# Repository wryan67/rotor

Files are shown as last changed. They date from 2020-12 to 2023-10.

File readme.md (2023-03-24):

Antenna Rotor Controller
------------------------
This program is designed to work with any rotor that uses a variable resistor for it's aspect indicator and limit swithes to prevent turning past the starting/stopping point.  Checkout the readme folder for display pinouts and a [[circuit diagram]](https://raw.githubusercontent.com/wryan67/rotor/main/schematics/drawio/rotor.png) for the system.

A special thanks to [PCBWay.com](http://www.pcbway.com) for supplying the professionally made PCB board!  

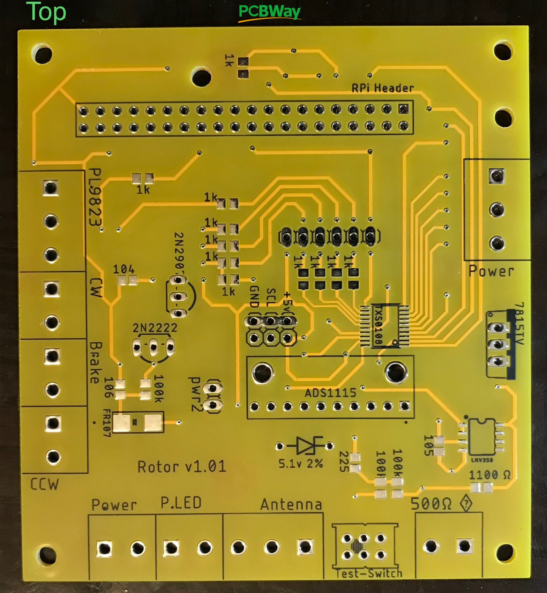
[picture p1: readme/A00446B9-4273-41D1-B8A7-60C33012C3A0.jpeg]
pcbway.com

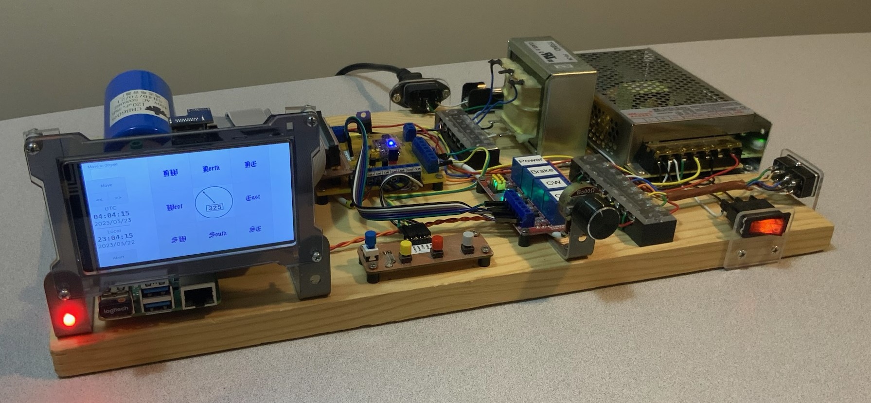
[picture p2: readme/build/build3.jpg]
build with pcbway.com


### Rotor Aspect Indicator
This system was designed around, and tested using a "Tail Twister" Model T2X - Rotator.  The Tail Twister utilizes a 500Ω variable resistor to ascertain the antenna's current direction.  The 500Ω variable resistor looks like this:  
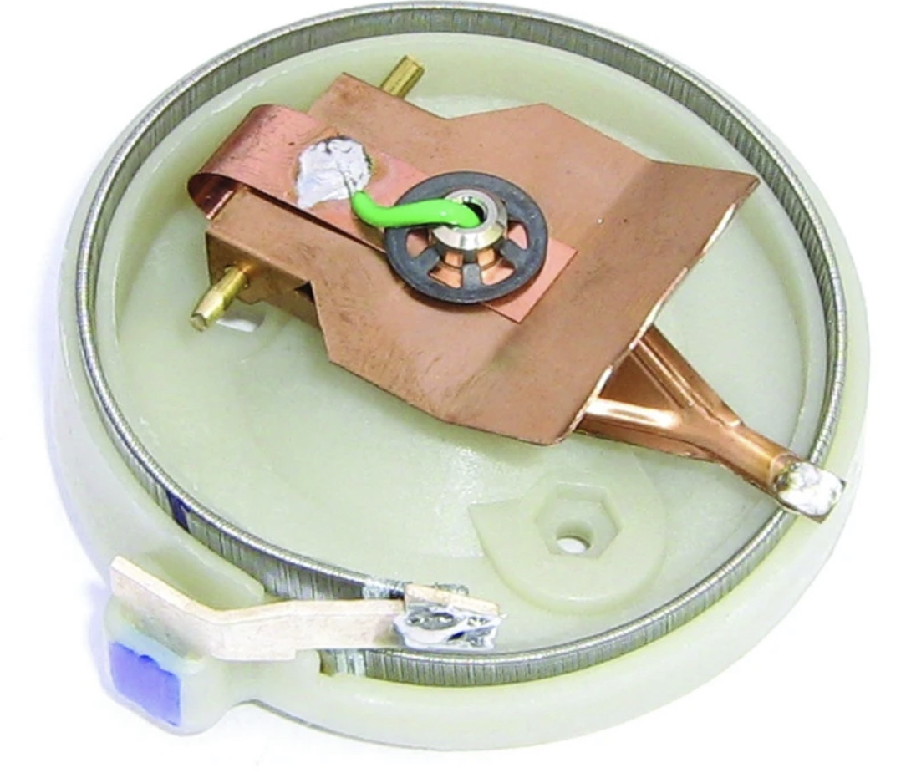
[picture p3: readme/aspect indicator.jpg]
aspect indicator


### Prerequisites:

Required system Libraries:

    $ sudo apt install libgtk-3-dev glade xdotool gawk ksh

Optional system Libraries:

    $ sudo apt vim tigervnc-standalone-server  tigervnc-xorg-extension tigervnc-scraping-server

## WiringPi

This step is required on RPi 4B.   Follow the instrctions on this website to upgrade to version 2.52

* http://wiringpi.com/wiringpi-updated-to-2-52-for-the-raspberry-pi-4b/

## Configuration

Using raspi-config, these options can be manuplated.  Enabling the I2C and SPI busses are required.

* System Options
  * Set the hostname
  * Set the pasword for the pi user
* Display Options
  * Disable screen blanking
* Interface Options
  * Enable the I2C bus
  * Enable the SPI bus
  * Enable the VNC server
  * Enable the SSH server

Starting raspi-config:

    $ sudo raspi-config

## Requirements

Overclocking the I2C bus is required to achive the desired 2500 samples per second.  Edit the /boot/config.txt file using:

Note: this step may need to be reapeated after installing a display device driver

    $ sudo vi /boot/config.txt 

Next, look for the i2c_arm parameter.  Note that if you've already enable the i2c bus via raspi-config, then you may have multiple lines in the config.txt file that have i2c_arm.  Look for the one that is uncommented.   If there are multiple "dtparam=i2c_arm=on" lines that are uncommented, comment out all but one.

    #dtparam=i2c_arm=on
    - or -
    dtparam=i2c_arm=on

Change it to:

    dtparam=i2c_arm=on,i2c_arm_baudrate=400000

## Disable warning lights
While you're in the boot config, you may want to disable the power indicator and lightning bolt indicator.  These indicators do not work properly on older RPi models due to an under sized capacitor on the RPi.  Newer models have larger capacitors, so if you have a brand new RPi 4, this step may not be necessary, but for the older RPi 4's, this indicator is extremely annoying. 

    $ sudo vi /boot/config.txt
    
    Append the following lines:
    
    # only affects power led operation
    dtparam=pwr_led_trigger=none
    dtparam=pwr_led_activelow=off
    # affects lightning bolt indicator
    avoid_warnings=1

### Required GIT Hub software:

Pleaase read the installation instructions carefully on each github project.  They're all similar, but non necessarially the same. 

* ADS1115 Library - https://github.com/wryan67/ads1115_rpi_lib    

      $ git clone https://github.com/wryan67/ads1115_rpi_lib.git

* NeoPixel Library - https://github.com/wryan67/neopixel_rpi_lib

       $ git clone https://github.com/wryan67/neopixel_rpi_lib.git       

* Log4Pi -https://github.com/wryan67/log4pi

       $ git clone https://github.com/wryan67/log4pi.git

### Download:

    git clone https://github.com/wryan67/rotor.git
    
### Compile:

    $ make
    
### Run:

Follow the instructions for autostart, then setup
    $ . scripts/set
    $ ./bin/rotor
    
### Auto Start on Boot

To start rotor on boot:

* Copy all files from the scripts folder (in this project) to $HOME/bin, then setup lxsession autostart using these commands:

      $ mkdir -p /home/pi/bin
      $ cp -p /home/pi/rotor/scripts/* /home/pi/bin
      $ cp -p /home/pi/rotor/bin/rotor /home/pi/bin
      $ cd /home/pi/bin
      $ sudo chown root rotor
      $ sudo chmod g+w  rotor
      $ sudo chmod u+s  rotor
      $ sudo chmod a+x  rotor
      $ mkdir -p ~/.config/lxsession/LXDE-pi/
      $ ln /home/pi/bin/autostart ~/.config/lxsession/LXDE-pi/autostart

### Build

This is the 2nd controller I built:
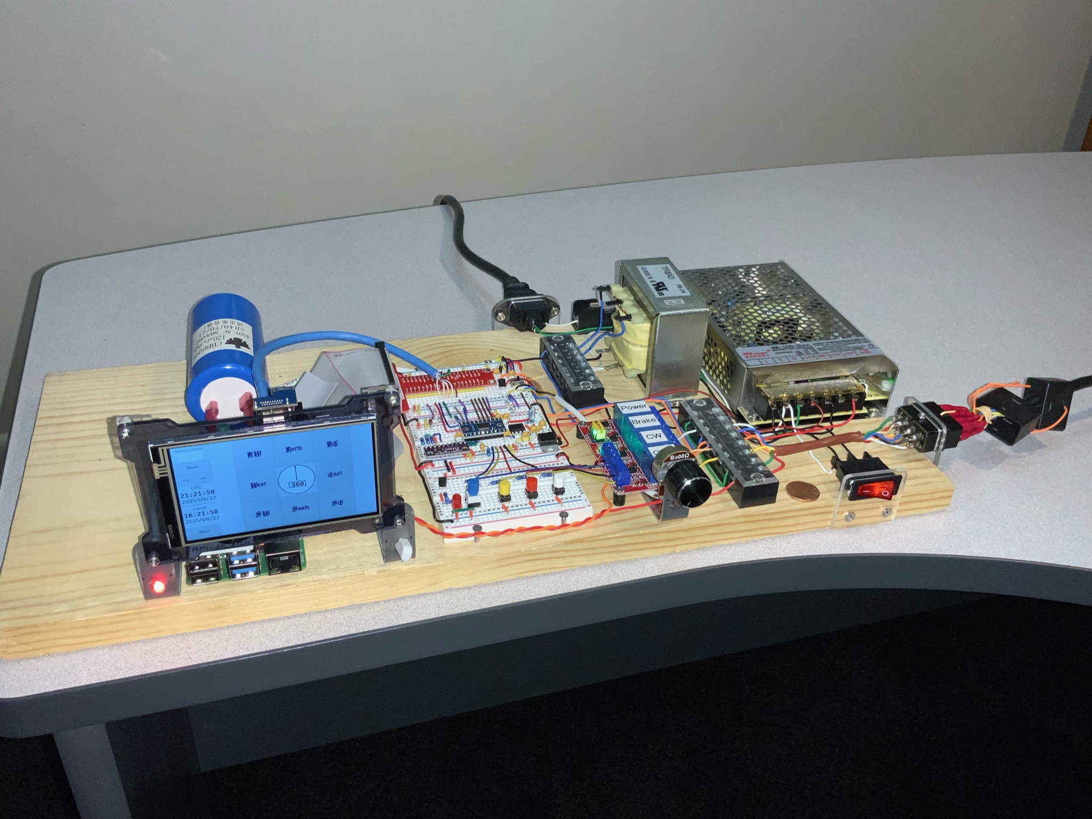
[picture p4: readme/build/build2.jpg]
build2


### Screenshots:

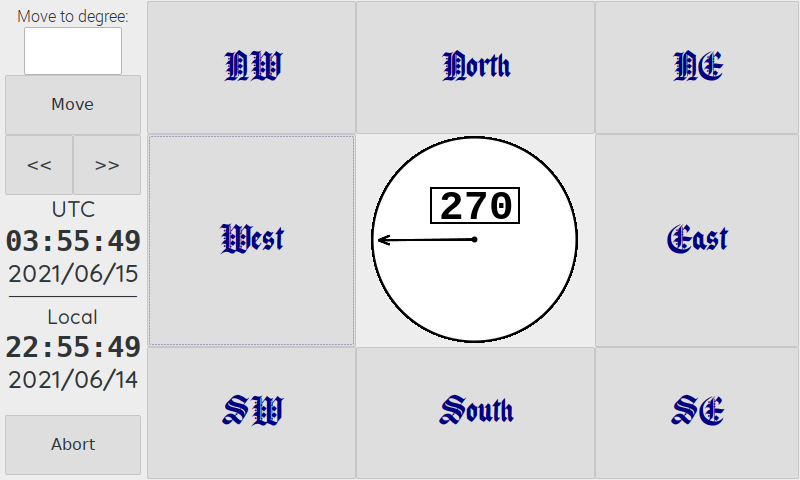
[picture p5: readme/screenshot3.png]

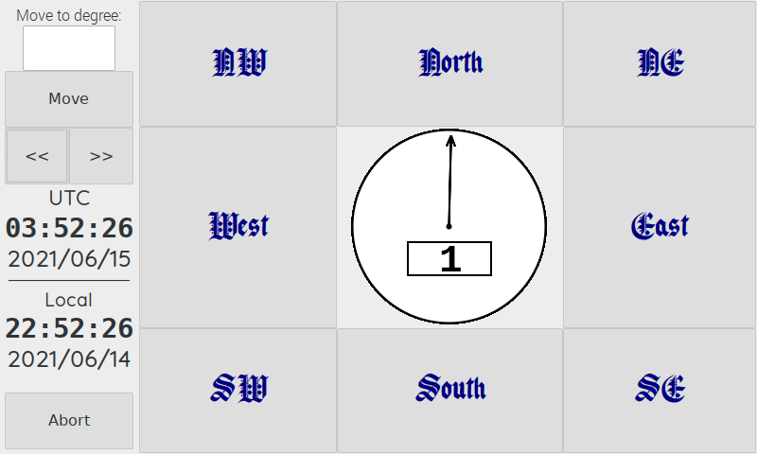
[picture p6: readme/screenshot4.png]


In order to access the configuration screens, click anywhere on the time clock.
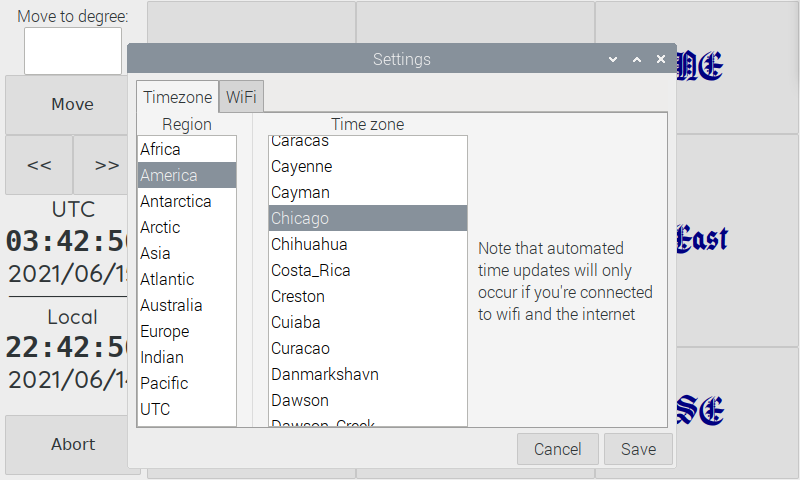
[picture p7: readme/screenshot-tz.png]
screenshot-tz

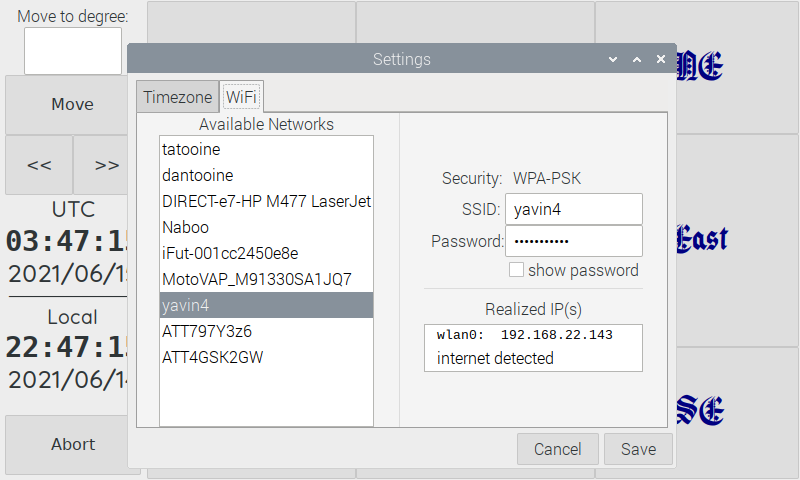
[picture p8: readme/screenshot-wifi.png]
screenshot-wifi


## Parts list
 
[Parts List](https://docs.google.com/spreadsheets/d/144g_11gsdxmeO28szwi-ss_1HRNR7ysNT9Fy6vf18YI/edit?usp=sharing)

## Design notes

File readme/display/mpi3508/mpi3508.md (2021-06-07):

## Driver install

https://github.com/goodtft/LCD-show

    $ git clone https://github.com/goodtft/LCD-show.git
    $ cd LCD-show
    $ sudo ./MPI3508-show

## Reference:  

https://raspberrypi.stackexchange.com/questions/61053/tft-lcd-3-5-display-with-inverted-axis

Invert instructions:

I had to swap both axis, and invert both of them as well, and then widen the input field
(reduce minx, increase max, reduce miny, increase maxy)

$ vi /etc/X11/xorg.conf.d/99-calibration.conf

    Section "InputClass"
    Identifier        "calibration"
    MatchProduct      "ADS7846 Touchscreen"
    Option "MinX"     "1834"
    Option "MaxX"     "62280"
    Option "MinY"     "61309"
    Option "MaxY"     "3738"
    Option "SwapXY"   "1" # unless it was already set to 1
    Option "InvertX"  "0"
    Option "InvertY"  "0"

    Option "TransformationMatrix" "0 -1 1 -1 0 1 0 0 1"

    EndSection

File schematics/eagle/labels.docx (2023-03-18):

J3

JP1

Console

+5 | +24 | Gnd

Gnd | P.SW | Gnd | P.led | Gnd | R.4 | R.3

LED
Ground
Power
CCW
Brake
CW

Ground
CW
Brake
CCW
Power
+5v

Gnd | +5v | Data | Gnd | CW | Gnd | Brk | Gnd | CCW

Data | Gnd

J10

Ads1115 addr

+5v
SCL
Gnd

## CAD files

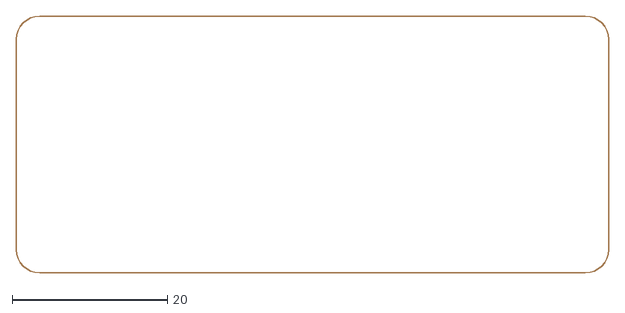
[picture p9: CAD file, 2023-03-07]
eagle/hat/hat.border.dxf
76.2 x 33.0

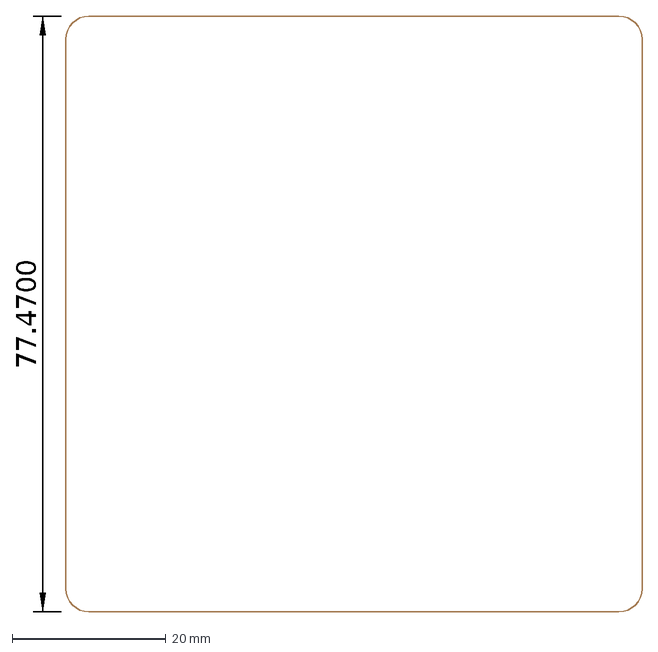
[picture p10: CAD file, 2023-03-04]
eagle/rotor.border.dxf
77.4700

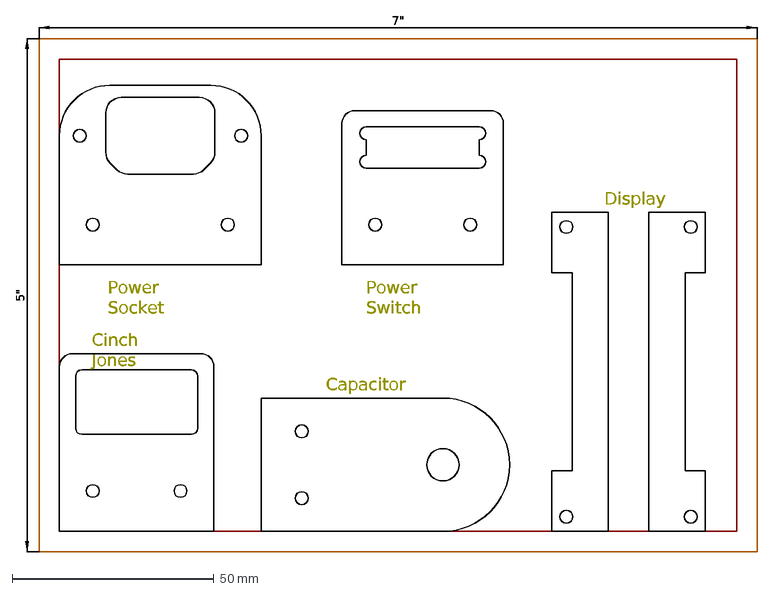
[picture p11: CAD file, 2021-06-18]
readme/rotor.brackets.dxf
7"
5"
Power Switch
Power Socket
Cinch Jones
Capacitor
Display

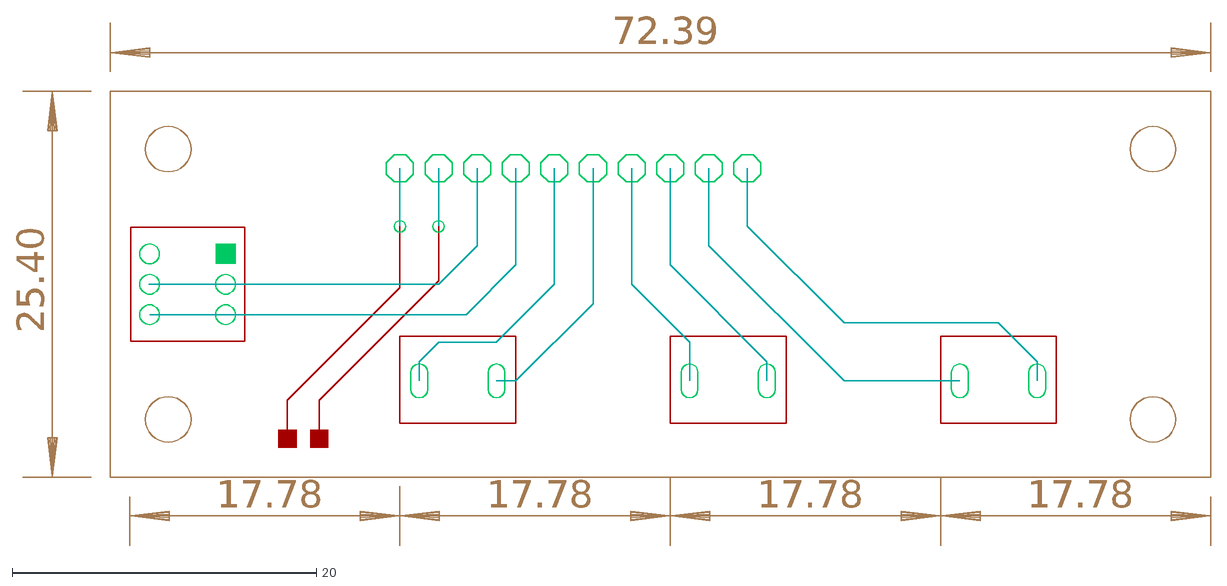
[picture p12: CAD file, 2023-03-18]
schematics/eagle/console/console.dxf
17.78
25.40
72.39

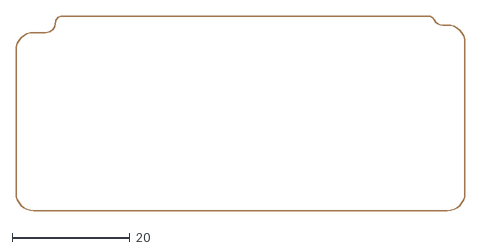
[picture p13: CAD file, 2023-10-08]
schematics/eagle/hat/hat.border.dxf
76.2 x 33.0

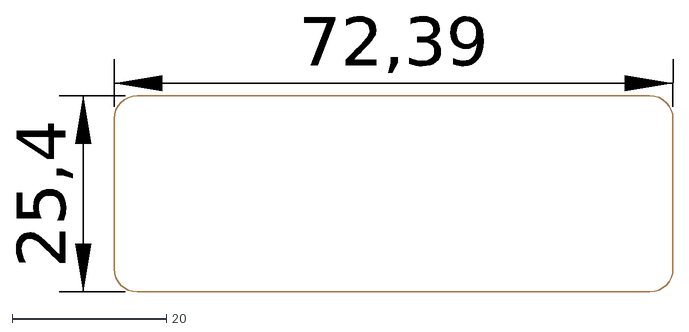
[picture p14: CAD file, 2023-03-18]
schematics/eagle/console/console.border.dxf
72,39
25,4

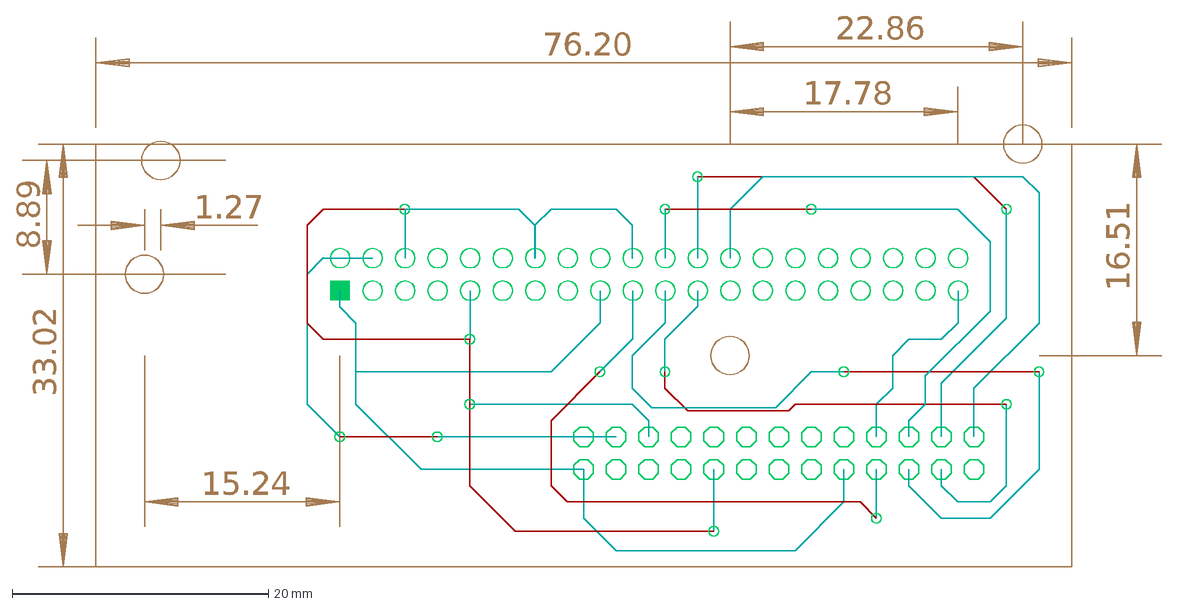
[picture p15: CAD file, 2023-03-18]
schematics/eagle/hat/hat.dxf
15.24
17.78
76.20
33.02
1.27
8.89
16.51
22.86

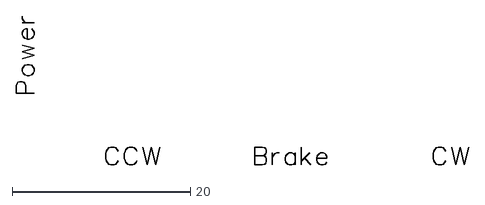
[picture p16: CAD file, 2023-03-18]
schematics/eagle/console/console.silkscreen.dxf
50.7 x 16.7

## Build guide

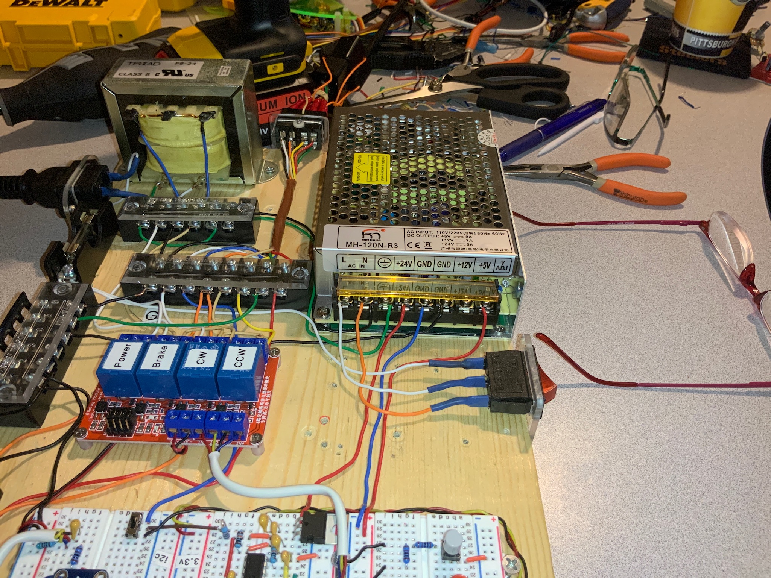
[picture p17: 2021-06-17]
readme/build/build1/01e3e5bd2f1fe0cc2b7c0081a9e1a19cae45f796dd.jpg

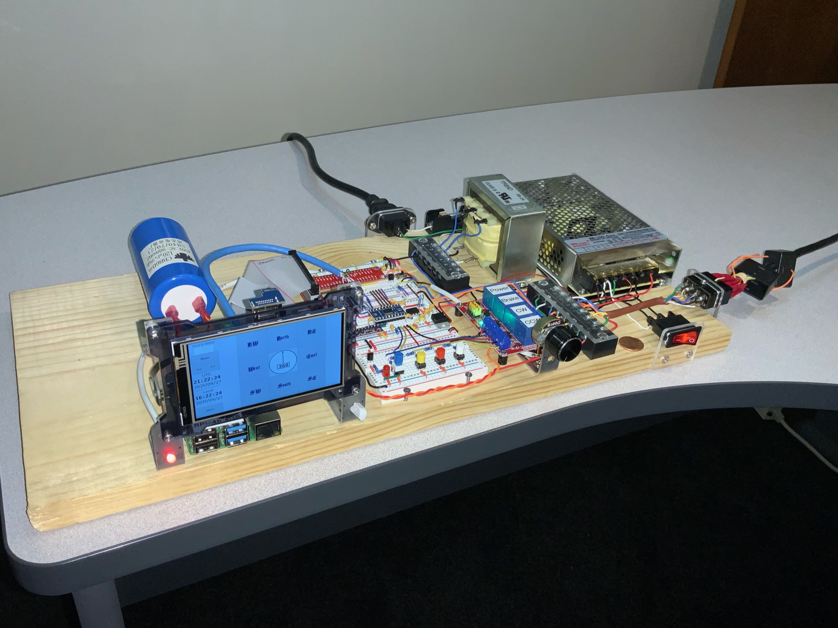
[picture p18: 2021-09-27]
readme/build/build2/0190c7da8ba504bc90833dc5dbd8328431b8305b7f.jpg

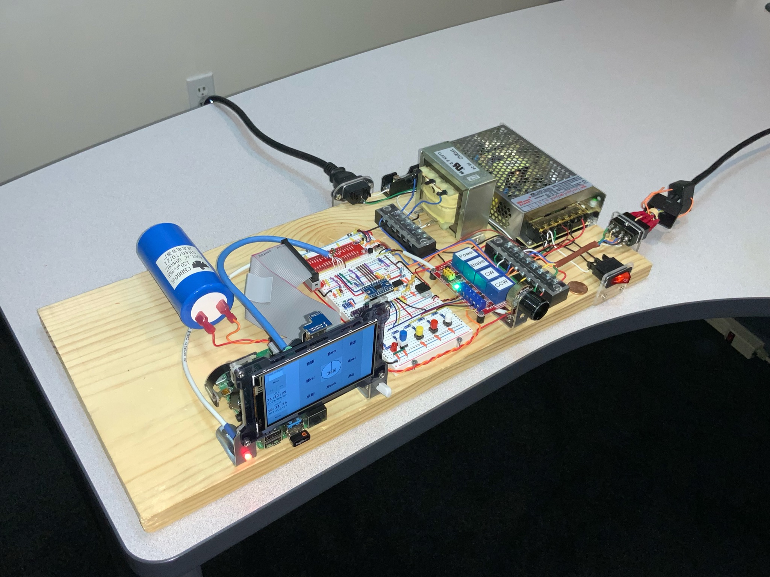
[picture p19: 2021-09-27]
readme/build/build2/0177888d93dca570d3d4cccc68184cede0cbc22092.jpg

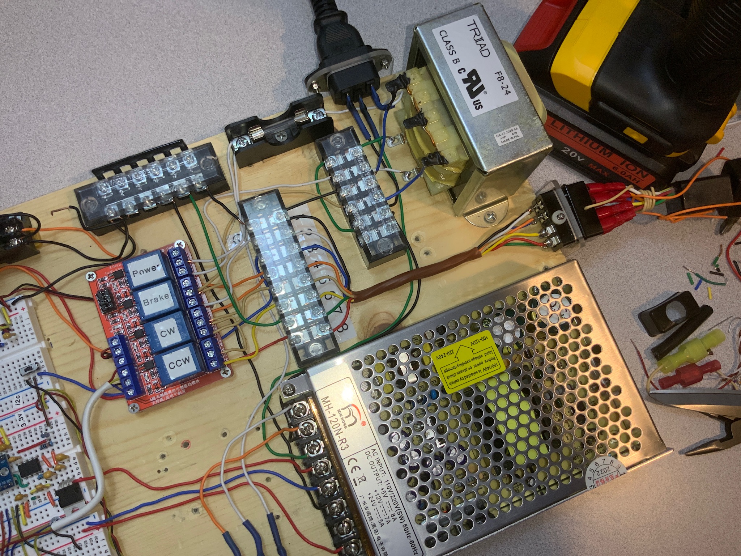
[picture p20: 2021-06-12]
readme/build/build1/0174a11db3228b720648c54a1771a86e80a43dbbdf.jpg

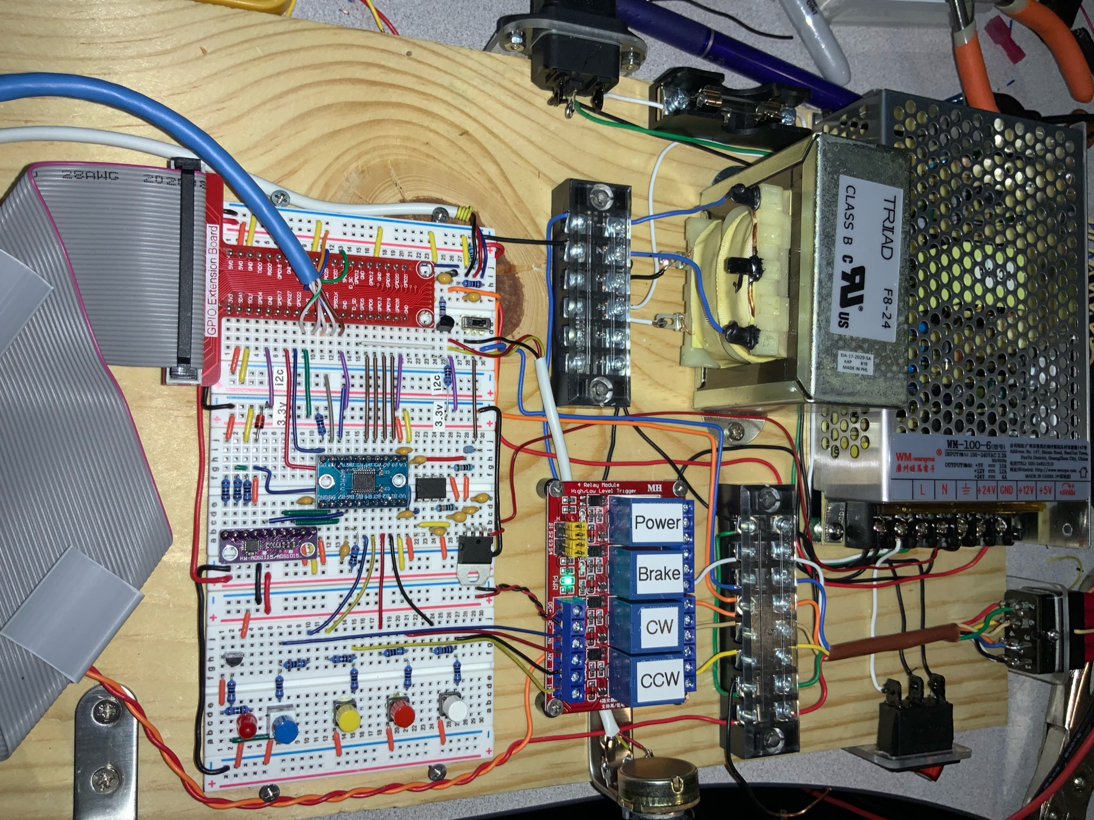
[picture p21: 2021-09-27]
readme/build/build2/01ecdf66102f84319e49356c2da052363e71326a41.jpg

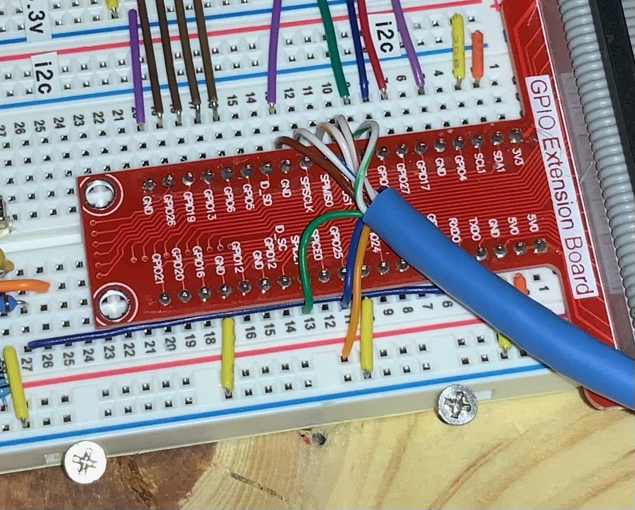
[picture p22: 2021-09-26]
readme/build/build2/015e3193f11c44bc42abcfa113b0f820811d2a1f84.jpg

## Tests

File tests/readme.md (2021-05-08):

* vc stands for voltage catcher
* vc for ads1115 is in the ads115 project (ads115_rpi_lib)
* $ ln -fs vc -> ../../ads1115_rpi_lib/example/vc .

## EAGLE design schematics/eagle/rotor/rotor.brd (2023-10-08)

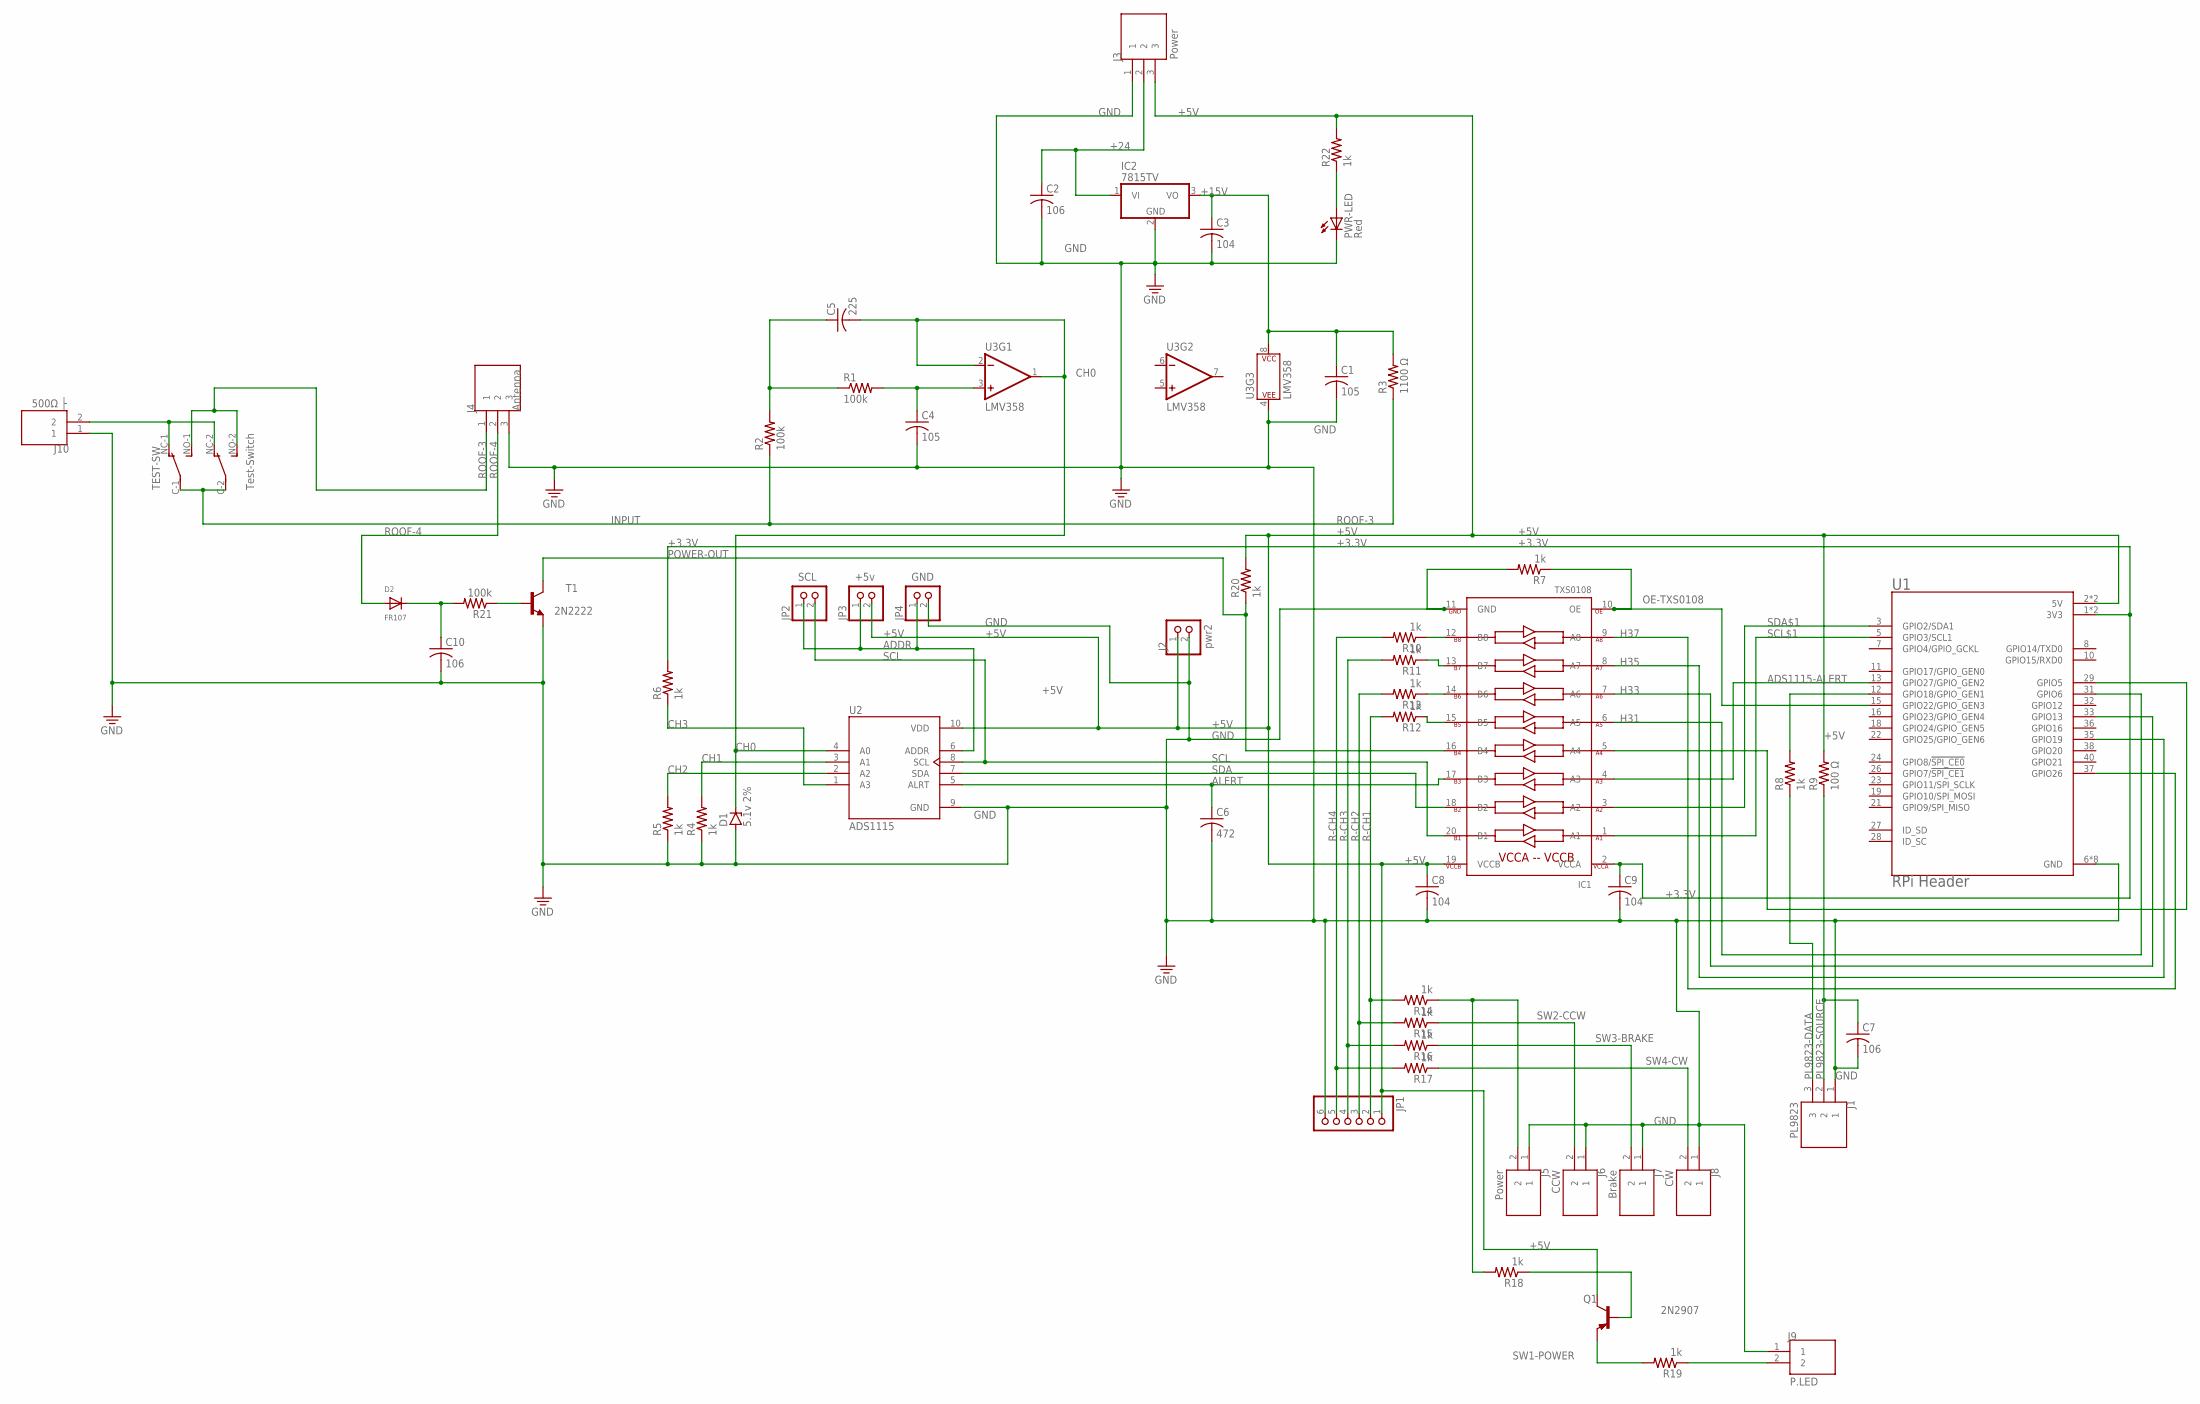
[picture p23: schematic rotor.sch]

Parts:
C1, C4: 105; C0805
C2, C7, C10: 106; C0805
C3, C8, C9: 104; C0805
C5: 225; C0805
C6: 472; C0805
D1: 5.1v 2%; ZDIO-7.5
D2: FR107; SMADIODE
IC1: TXS0108; TSSOP20
IC2: 7815TV; TO220V
J1: PL9823; CUI_TB004-508-03BE
J2: pwr2; 1X02
J3: Power; CUI_TB004-508-03BE
J4: Antenna; CUI_TB004-508-03BE
J5: Power; CUI_TB004-508-02BE
J6: CCW; CUI_TB004-508-02BE
J7: Brake; CUI_TB004-508-02BE
J8: CW; CUI_TB004-508-02BE
J9: P.LED; CUI_TB004-508-02BE
J10: 500Ω ├; CUI_TB004-508-02BE
JP1: PINHD-1X6; 1X06
JP2: SCL; 1X02-SPECIAL
JP3: +5v; 1X02-SPECIAL
JP4: GND; 1X02-SPECIAL
PWR-LED: Red; CHIP-LED0805
Q1: 2N2907; TO92-EBC-OVAL
R1, R2, R21: 100k; M0805
R3: 1100 Ω; M0805
R4, R5, R6, R7, R8, R10, R11, R12, R13, R14, R15, R16, R17, R18, R19, R20, R22: 1k; M0805
R9: 100 Ω; M0805
T1: 2N2222; TO92-EBC-OVAL
TEST-SW: Test-Switch; DP-DT
U1: RPi Header; MODULE_RASPBERRY_PI_3B+_HDR
U2: ADS1115; MODULE_1115_NARROW
U3: LMV358; SO08

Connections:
+3.3V: C9.1, IC1.2 (VCCA), R6.2, U1.1 (3V3), U1.17 (3V3)
+5V: C8.1, IC1.19 (VCCB), J2.1, J3.3, JP1.1, JP3.2, Q1.C, R9.2, R20.2, R22.2, U1.2 (5V), U1.4 (5V), U2.10 (VDD)
+15V: C1.1, C3.1, IC2.3 (VO), R3.2, U3.8 (P$V+)
+24: C2.1, IC2.1 (VI), J3.2
ADDR: JP2.1, JP3.1, JP4.1, U2.6 (ADDR)
ADS1115-ALERT: IC1.4 (A3), U1.13 (GPIO27/GPIO_GEN2)
ALERT: C6.1, IC1.17 (B3), U2.5 (ALRT)
CH0: C5.2, D1.C, U2.4 (A0), U3.1 (OUT), U3.2 (-IN)
CH1: R4.2, U2.3 (A1)
CH2: R5.2, U2.2 (A2)
CH3: R6.1, U2.1 (A3)
GND: C1.2, C2.2, C3.2, C4.2, C6.2, C7.2, C8.2, C9.2, C10.2, D1.A, IC1.11 (GND), IC2.2 (GND), J1.1, J2.2, J3.1, J4.3, J5.1, J6.1, J7.1, J8.1, J9.1, J10.1, JP1.6, JP4.2, PWR-LED.C, R4.1, R5.1, R7.2, T1.E, U1.6 (GND), U1.9 (GND), U1.14 (GND), U1.20 (GND), U1.25 (GND), U1.30 (GND), U1.34 (GND), U1.39 (GND), U2.9 (GND), U3.4 (P$V-)
H31: IC1.6 (A5), U1.31 (GPIO6)
H33: IC1.7 (A6), U1.33 (GPIO13)
H35: IC1.8 (A7), U1.35 (GPIO19)
H37: IC1.9 (A8), U1.37 (GPIO26)
INPUT: R2.1, R3.1, TEST-SW.C-1, TEST-SW.C-2
unnamed: C4.1, R1.2, U3.3 (+IN)
unnamed: R8.2, U1.12 (GPIO18/GPIO_GEN1)
unnamed: C5.1, R1.1, R2.2
unnamed: IC1.15 (B5), R12.1
unnamed: IC1.14 (B6), R13.1
unnamed: IC1.13 (B7), R11.1
unnamed: IC1.12 (B8), R10.1
unnamed: Q1.E, R19.2
unnamed: Q1.B, R18.1
unnamed: IC1.5 (A4), U1.29 (GPIO5)
unnamed: C10.1, D2.C, R21.2
unnamed: R21.1, T1.B
unnamed: PWR-LED.A, R22.1
unnamed: J10.2, TEST-SW.NC-1, TEST-SW.NC-2
OE-TXS0108: IC1.10 (OE), R7.1, U1.15 (GPIO22/GPIO_GEN3)
PL9823-DATA: J1.3, R8.1
PL9823-SOURCE: C7.1, J1.2, R9.1
POWER-OUT: IC1.16 (B4), R20.1, T1.C
R-CH1: JP1.2, R12.2, R14.2
R-CH2: JP1.3, R13.2, R15.2
R-CH3: JP1.4, R11.2, R16.2
R-CH4: JP1.5, R10.2, R17.2
ROOF-3: J4.1, TEST-SW.NO-1, TEST-SW.NO-2
ROOF-4: D2.A, J4.2
ROTOR-PWR-LED-SOURCE: J9.2, R19.1
SCL: IC1.20 (B1), JP2.2, U2.8 (SCL)
SCL$1: IC1.1 (A1), U1.5 (GPIO3/SCL1)
SDA: IC1.18 (B2), U2.7 (SDA)
SDA$1: IC1.3 (A2), U1.3 (GPIO2/SDA1)
SW1-POWER: J5.2, R14.1, R18.2
SW2-CCW: J6.2, R15.1
SW3-BRAKE: J7.2, R16.1
SW4-CW: J8.2, R17.1

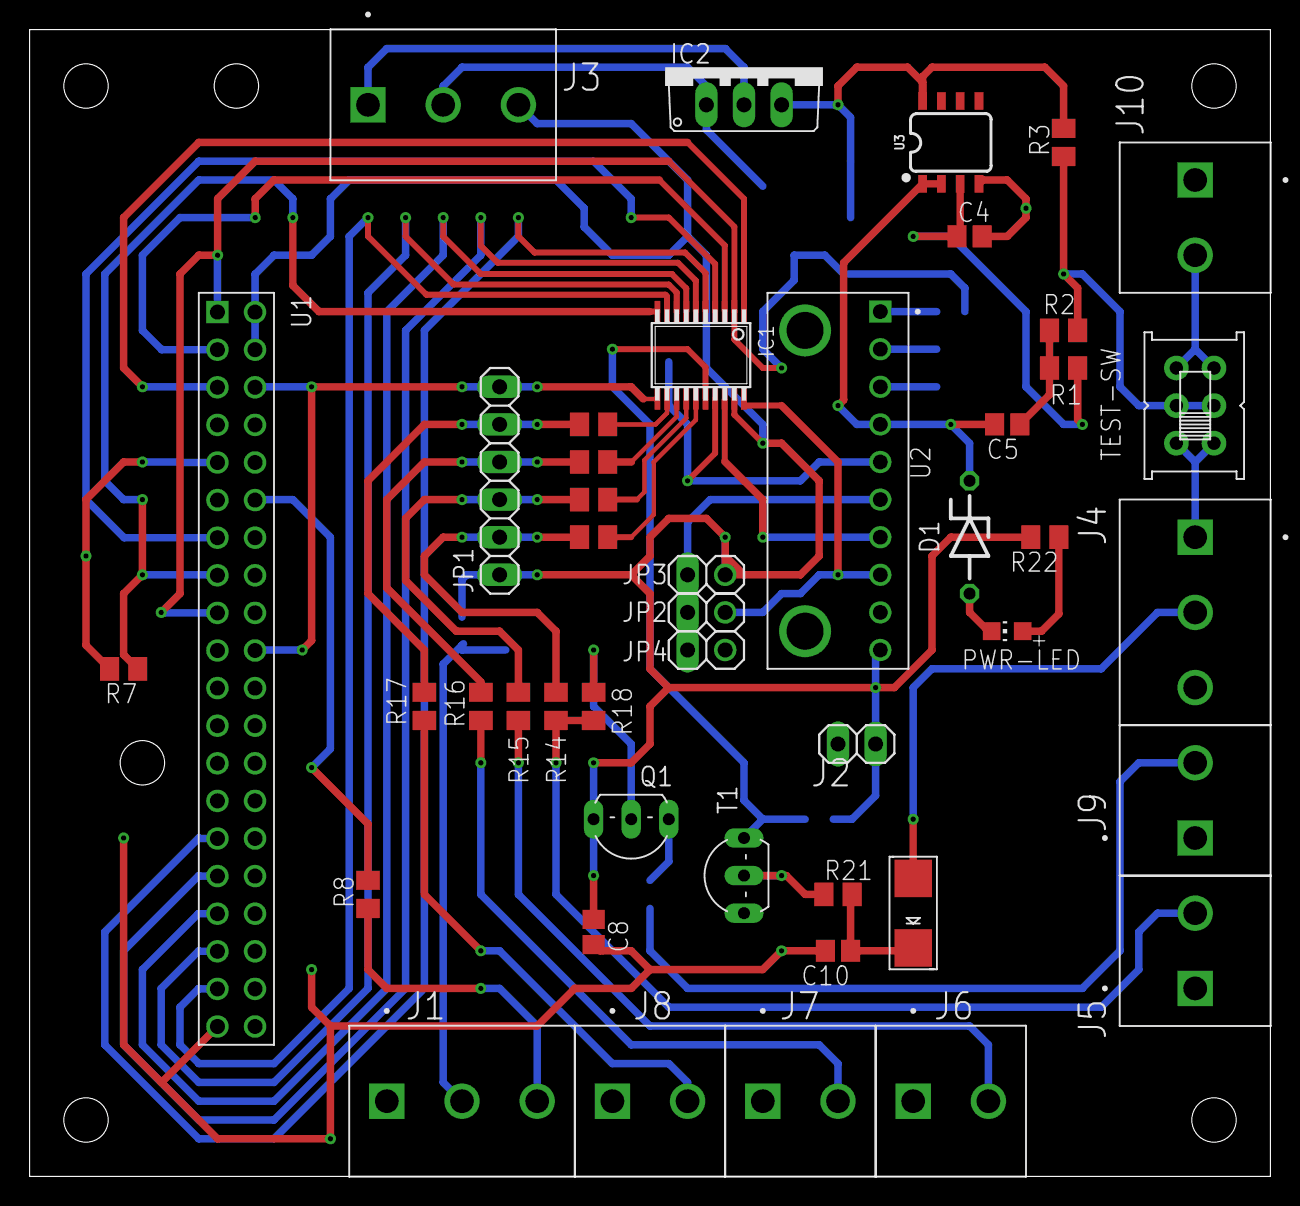
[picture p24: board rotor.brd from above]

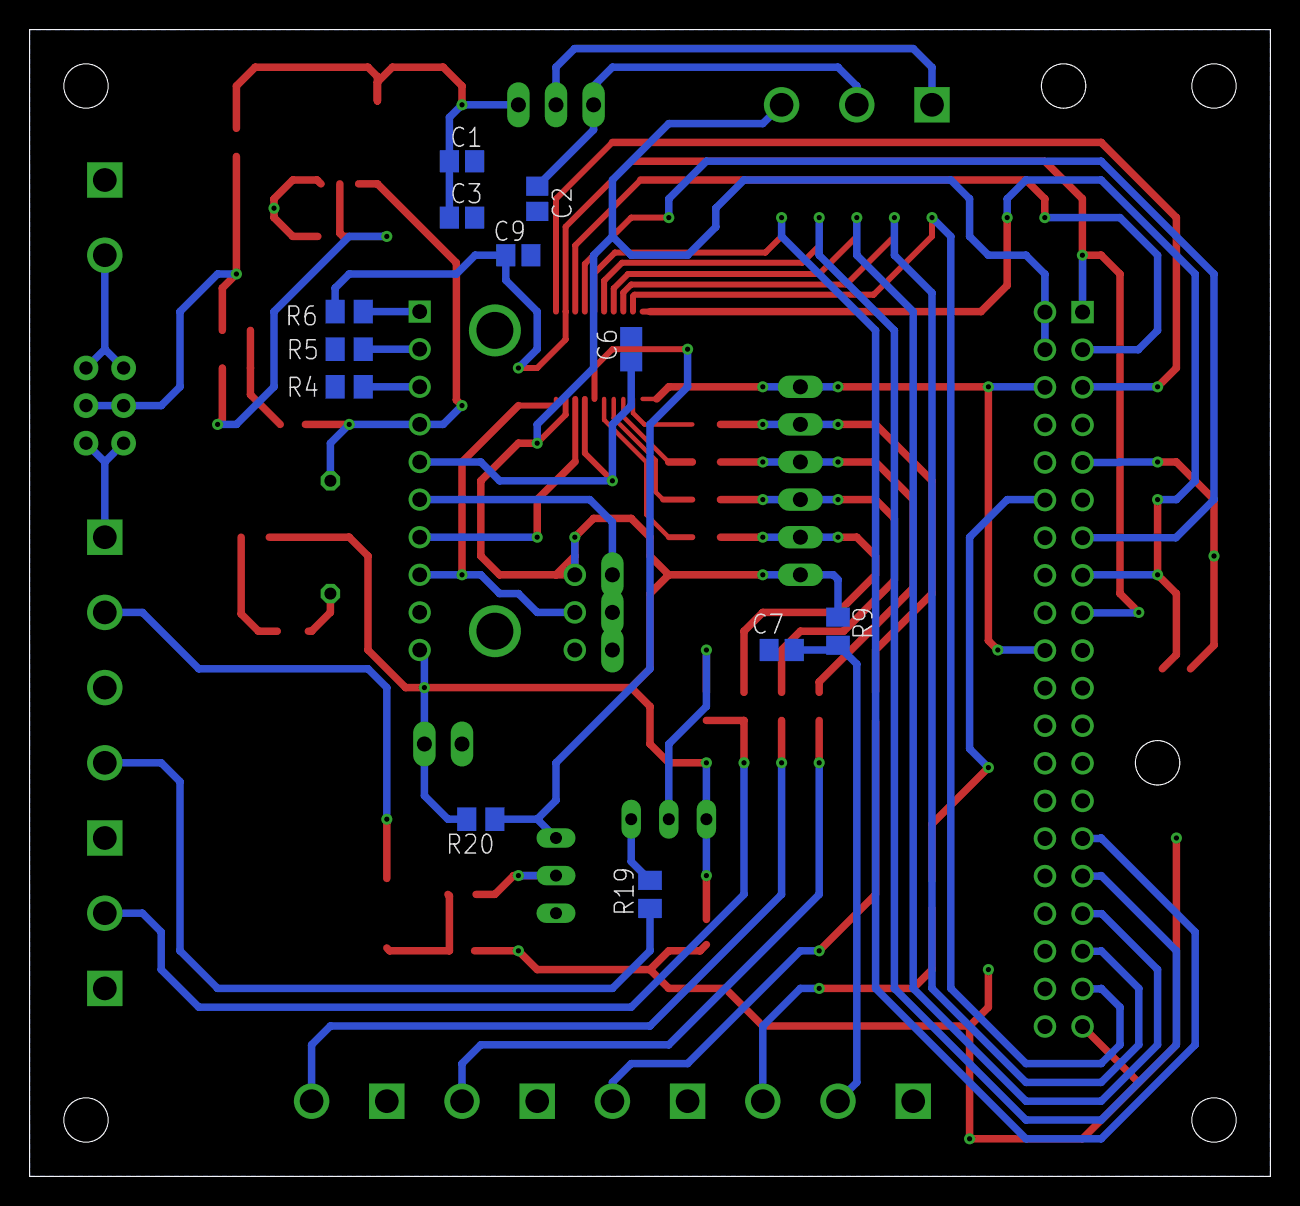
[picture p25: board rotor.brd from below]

Board: 2 copper layers, 83.8 x 77.5 mm, 57 parts (12 on the bottom side), 50 nets.

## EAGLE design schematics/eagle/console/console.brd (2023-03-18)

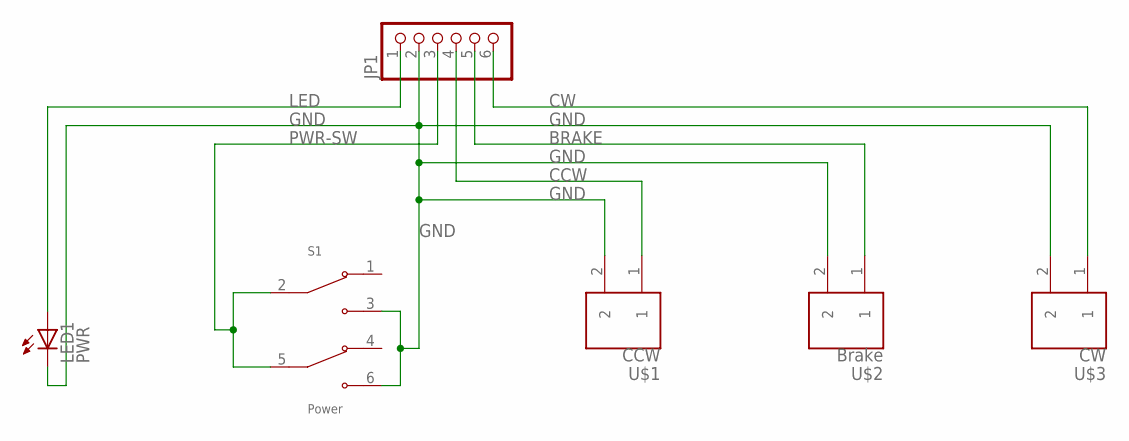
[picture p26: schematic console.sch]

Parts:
JP1: PINHD-1X6; 1X06
LED1: PWR; CHIPLED_0805
S1: Power; IM211
U$1: CCW; SPST-5MM
U$2: Brake; SPST-5MM
U$3: CW; SPST-5MM

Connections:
BRAKE: JP1.5, U$2.1
CCW: JP1.4, U$1.1
CW: JP1.6, U$3.1
GND: JP1.2, LED1.C, S1.3 (NO1), S1.6 (NO2), U$1.2, U$2.2, U$3.2
LED: JP1.1, LED1.A
PWR-SW: JP1.3, S1.2 (COM1), S1.5 (COM2)

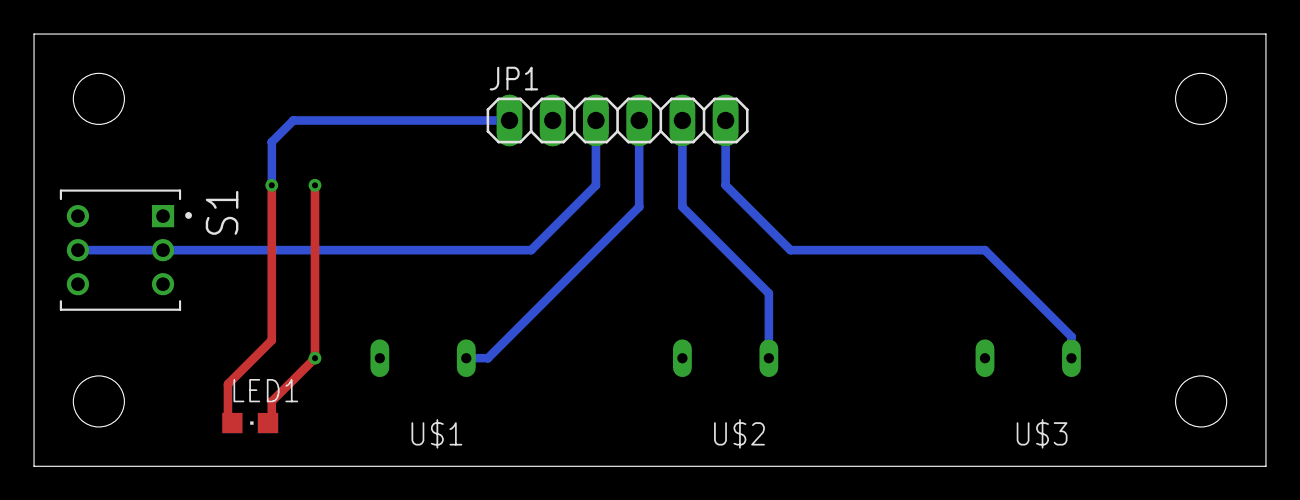
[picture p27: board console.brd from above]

Board: 2 copper layers, 72.4 x 25.4 mm, 6 parts (0 on the bottom side), 6 nets.

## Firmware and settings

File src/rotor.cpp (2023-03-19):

#include <gtk/gtk.h>
#include <math.h>
#include <thread>

#include <wiringPi.h>
#include <wiringPiI2C.h>
#include <ads1115rpi.h>
#include <neopixel.h>  
#include <atomic>
#include <vector>
#include <mutex>
#include <algorithm>
#include <utility>

#include <time.h>
#include <sys/time.h>


#include "motor.h"
#include "Options.h"

using namespace std;
using namespace common::utility;
using namespace common::synchronized;

Options options = Options();
bool debug=false;

char configFolder[2048];

#define BASE 200
#define SPI_CHAN 0
#define MCP3008_SINGLE  8
#define MCP3008_DIFF    0

int screenBreakpoint=320;

bool cwLimitPoint=false;
int  ADS1115_ADDRESS=0x48;
int  a2dHandle=-1;

bool parked=true;
FILE *logFile=nullptr;

float calibrationA;
float calibrationB;
float calibrationC;
  int calibrationEast, calibrationWest;

vector<pair<uint64_t, float>*> points;
bool capturePoints=false;

int screenWidth;
int screenHeight;

bool skipWindow = false;
long long skipTime = 0;

#define TARGET_FREQ             WS2811_TARGET_FREQ
#define GPIO_PIN                18   // BCM numbering system
#define DMA                     10   // DMA=Direct Memory Access
int  led_count =                 1;  // number of pixels in your led strip
int  operationIndicator = 0;
int  stopColor    = 0xff0000;
int  movingColor  = 0x00ff00;
int  brakingColor = 0xffff00;


// #pragma clang diagnostic push
// #pragma clang diagnostic ignored "-Wdeprecated-declarations"
#pragma GCC diagnostic push
#pragma GCC diagnostic ignored "-Wdeprecated-declarations"

Logger     logger("main");

atomic<bool> stoppingRotor{false};
atomic<bool> isSettingsDialogueActive{false};
atomic<bool> calledHideSettings{false};
atomic<bool> showingRealizedIp{false};
atomic<bool> showingWifiUpdates{false};
atomic<bool> detectingIntenet{false};
bool hasInternet{false};

vector<string> realizedIPs;
vector<string> wifiNetworks;


GtkWidget *drawingArea=nullptr;
GtkWidget *timeWindow=nullptr;
GObject   *mainWindow=nullptr;

GtkLabel  *utcLabel=nullptr;
GtkLabel  *utcTime=nullptr;
GtkLabel  *utcDate=nullptr;

char       utcTimeBuffer[512];
char       utcDateBuffer[512];

GtkLabel  *timeSeparator=nullptr;
GtkLabel  *localLabel=nullptr;
GtkLabel  *localTime=nullptr;
GtkLabel  *localDate=nullptr;

char       localTimeBuffer[512];
char       localDateBuffer[512];

GtkBuilder *settingsBuilder;
GtkWindow  *settingsWindow;
GtkListBox *countryListBox;
GtkListBox *timezoneListBox;
GtkListBox *availableNetworksListBox;
gulong      availableNetworksListBoxSignal;
GtkEntry   *ssidEntry;
GtkEntry   *passwdEntry;
GtkCheckButton *showPasswd;

vector<string> systemCountries;
vector<string> systemTimezones;
vector<string> timezones;
vector<string> countries;
char currTimezone[4096];

float currentVolts=-1;
float rotorDegree=0;
bool  forceCompassRedraw=false;
bool  forceVoltageDebugDisplay=false;

mutex displayLock;
mutex pickSSID;
mutex conversionInProgress;

GtkWidget *degreeInputBox;

static cairo_surface_t *surface = NULL;
static void drawCompass(bool newSurface);
static void createDrawingSurface(GtkWidget *widget);

char degreeTextBox[32];
bool ignoreMargins=false;

int           sampleMode=-1;
unsigned int  windowSize=0;
float         totalSampleVolts=0;
long          totalSamples;
float         lastDisplayVolts=-9;
vector<float> samples;
float         cableDisconnectedVolts;

struct directionalType {
  int east,  se, south,   sw, west,  nw, north, ne;
} directional = {
        90, 135,   180,  225,  270, 315,     0, 45
};

float getDegree(float volts);

float translateRotor2Display(float degrees) {
    if (degrees<180) {
        return degrees+180;
    } else {
        return degrees-180;
    }
}

float translateDisplay2Rotor(float degrees) {
    float workingDegrees=degrees-180;
    if (workingDegrees<0) {
        workingDegrees+=360;
    }    
    return workingDegrees;
}

void getScreenResolution() {
  // old: 480x320
  // new: 800x480


  GdkRectangle workarea = {0};
  gdk_monitor_get_workarea(
  gdk_display_get_primary_monitor(gdk_display_get_default()),
    &workarea);

  screenWidth=workarea.width;
  screenHeight=workarea.height;

  logger.debug("screen width x height: %d x %d", screenWidth, screenHeight);

  if (screenWidth<480 || screenHeight<320) {
    logger.error("minimum screen resolution is 840x320");
    exit(7);
  }
}

void hideMouse() {
  char cmd[2048];
  delay(1000);
  sprintf(cmd,"xdotool mousemove %d %d", screenWidth, screenHeight);
  system(cmd);
}

// float lastVolts=999;
long long lastConversion=-1;

void voltageCatcher() {
  if (!conversionInProgress.try_lock()) {
    return;
  }

  float volts = readVoltage(a2dHandle);
  currentVolts=volts;
  

  switch (sampleMode) {
    case -1: {
      conversionInProgress.unlock();
      return;
    }
    case 0: {
      ++windowSize;
      conversionInProgress.unlock();
      return;
    }
    case 1: {
      totalSampleVolts+=volts;      
      samples.push_back(volts);

      if (samples.size()>=windowSize) {
        ++sampleMode;
      }      
    }
    case 2: {
      if (lastConversion<0) lastConversion=currentTimeMillis();

      if (skipWindow) {
        long long now = currentTimeMillis();
        if (now<skipTime) {
          conversionInProgress.unlock();
          return;
        }
        skipWindow=false;
      }
      
      totalSampleVolts+=volts;      
      samples.push_back(volts);

      auto oldestSample = samples.at(0);
      totalSampleVolts-=oldestSample;
      samples.erase(samples.begin());

      float volts = totalSampleVolts / (float)windowSize;

      float newDegree = getDegree(volts);

      if (abs(newDegree)>360) {
          newDegree=360;
      }
      if (newDegree<0) {
          newDegree=0;
      }
      int lastDegree=rotorDegree;
      rotorDegree=newDegree;

      if (abs(newDegree-lastDegree)>options.wobbleLimit) {
          forceVoltageDebugDisplay=true;
          lastDegree=newDegree;
      }

      if (abs(volts-lastDisplayVolts)>0.05 || forceVoltageDebugDisplay) {
          int limitSwitch = digitalRead(options.LimitSwitch);

          logger.debug("bs=%d ls=%d ch[0]=%.3f i-degree=%.1f d-degree=%.0f gain=%d r1=%d", 
                  getBrakeStatus(), limitSwitch,  volts, newDegree, translateRotor2Display(newDegree), 
                  options.gain, options.aspectFixedResistorOhms);
          lastDisplayVolts=volts;
          forceVoltageDebugDisplay=false;
      }
      conversionInProgress.unlock();
      return;
    }
  }
  conversionInProgress.unlock();

}


atomic<bool> cableDisconnectDialogActive{false};
bool cableMonitorMessageWritten=false;

void resetCableDisconnectWarning() {
  delay(2500);
  cableMonitorMessageWritten=false;
}

int showCableDisconnect(gpointer data) {
  bool expect=false;
  if (!cableDisconnectDialogActive.compare_exchange_strong(expect,true)) {
    return false;
  }

  char message[4096] = "\nThe cable is disconnected";

  if (currentVolts > 5.28) {
    sprintf(message,
              "The cable is disconnected\n" 
              "The ADS1115 chip cannot accept\n" 
              "voltage higher than 5.3 volts.\n"
              "current voltage is %.2g volts", currentVolts
    );
  }

  GtkDialogFlags flags = GTK_DIALOG_DESTROY_WITH_PARENT;
  GtkWidget *dialog = gtk_message_dialog_new ((GtkWindow*)mainWindow,
                            flags,
                            GTK_MESSAGE_ERROR,
                            GTK_BUTTONS_CLOSE,
                            message);

  gtk_window_set_title((GtkWindow*)dialog,"cable status");
  gtk_dialog_run((GtkDialog*)dialog);
  gtk_widget_destroy (dialog);
  cableDisconnectDialogActive=false;

  thread(hideMouse).detach();
  thread(resetCableDisconnectWarning).detach();


  return false;
}



void cableMonitor() {

  logger.debug("cable disconnect volts = %f", cableDisconnectedVolts);
  
  while (true) {
    if (currentVolts > cableDisconnectedVolts) {
      if (!cableMonitorMessageWritten && mainWindow!=nullptr) {
        logger.info("cable disconnnected");
        cableMonitorMessageWritten=true;


        g_idle_add(showCableDisconnect, nullptr);

      }
    } else {
      cableMonitorMessageWritten=false;
    }
    delay(100);
  }
}

struct MessageWindowData {
  const char     *title;
  const char     *message;
  bool            terminate;
  GtkApplication *app;
  GtkWindow      *parent;
};



void gtkWindow(gpointer data) {
  MessageWindowData *msg = (MessageWindowData*) data;
 
  GtkWidget *dialog = gtk_message_dialog_new ((GtkWindow*)mainWindow,
      GTK_DIALOG_DESTROY_WITH_PARENT,
      GTK_MESSAGE_ERROR,
      GTK_BUTTONS_CLOSE,
      msg->message
  );
  if (msg->parent!=nullptr) {
    gtk_window_set_transient_for((GtkWindow*)dialog,msg->parent);
  }
  getScreenResolution();
  thread(hideMouse).detach();

  gtk_window_set_title((GtkWindow*)dialog, msg->title);
  gtk_dialog_run((GtkDialog*)dialog);
  gtk_widget_destroy (dialog);

}

void softError(const char* title, const char *message, GtkWindow* parent) {
  MessageWindowData *data = new MessageWindowData;

  data->message=(char*)message;
  data->title=(char*)title;
  data->terminate=false;
  data->parent=parent;

  gtkWindow(data);
  delete data;
}

void gtkAppWindow(GtkApplication *app, gpointer data) {
  gtk_application_window_new(app);

  gtkWindow(data);
  g_application_quit(G_APPLICATION(app));
}


void applicaitonMessageWindow(MessageWindowData *msg) {

  GtkApplication *app = gtk_application_new ("org.rotor", G_APPLICATION_FLAGS_NONE);
  msg->app=app;

  g_signal_connect    (app, "activate", G_CALLBACK (gtkAppWindow), msg);
  g_application_run   (G_APPLICATION (app), 0, nullptr);
  g_object_unref      (app);

}

void bootError(const char *message) {
  MessageWindowData *error = new MessageWindowData;

  logger.error(message);
  error->message=message;
  error->title="boot failed";
  error->terminate=true;
  error->parent=nullptr;

  applicaitonMessageWindow(error);
  delete error;

  exit(4);
}


void a2dSetup() {
    cableDisconnectedVolts = (options.zenerDiode * (1-(options.zenerDiodeTolerance/100.0)))-0.01;

    a2dHandle = getADS1115Handle(ADS1115_ADDRESS);

    if (a2dHandle<0) {
        fprintf(stderr, "opening ads1115 failed: %s\n", strerror(errno));
        exit(3);
    }
    char *bootOverride = getenv("BOOTOVERRIDE");
    if (bootOverride) {
      return;
    }



    float v3 = readVoltageSingleShot(a2dHandle, options.v3channel, 0);


    if (abs((3.3-v3)/((3.3+v3)/2))>0.10) {
        for (int c=0;c<4;++c) {
            float volts = readVoltageSingleShot(a2dHandle, c, 0);
            logger.info("channel<%d>=%f", c, volts);
        }
        logger.info("a2dHandle=%d; a2d_address=%02x", a2dHandle, ADS1115_ADDRESS);
        logger.info("voltage on channel a%d=%f", options.v3channel, v3);
        logger.error("ads1115 chip is not working");

        char message[2048];
        sprintf(message, "The ADS1115 a2d chip does not appear to be functional on address 0x%02x", 
                      ADS1115_ADDRESS);
     
        bootError(message);
    }

    // options.sps=5;

// 0 : 000 : 8 SPS
// 1 : 001 : 16 SPS
// 2 : 010 : 32 SPS
// 3 : 011 : 64 SPS
// 4 : 100 : 128 SPS (default)
// 5 : 101 : 250 SPS
// 6 : 110 : 475 SPS
// 7 : 111 : 860 SPS

    unsigned int ads1115SPS[8] = { 8, 16, 32, 64, 128, 250, 475, 860 };

    unsigned int expectedSPS = 0.95*ads1115SPS[options.sps];
    logger.info("channel=%d; gain=%d; sps=%d", options.aspectVoltageChannel, options.gain, ads1115SPS[options.sps]);

    int   tries=3;

    wiringPiISR(options.a2dDataReady,INT_EDGE_FALLING, voltageCatcher);
    setADS1115ContinuousMode(a2dHandle, options.aspectVoltageChannel, options.gain, options.sps);

    // float targetPeriods = 3;
    // float sixtyHzPeriod = 1000.0 * ( 1.0 / 60.0); // 1000 ms * 1/60;
    // float targetWindow  = sixtyHzPeriod / 4;  // 60Hz period / 4;  //ms   4.2 ms

    // logger.info("60Hz period = %.1fms; targetPeriods=%.0f; targetWindow=%.1fms", sixtyHzPeriod, targetPeriods, targetWindow);

 
    long long elapsed;
    unsigned int savedSize;

    while (tries-->0) {
      delay(100);

      windowSize=0;
      totalSampleVolts=0;
      totalSamples=0;
      lastDisplayVolts=-9;
      samples.clear();
      forceVoltageDebugDisplay=false;
    
      skipWindow=false;
      ++sampleMode;
      auto startTime = currentTimeMillis();

      usleep(1000*1000);
      savedSize = windowSize;
      elapsed  = currentTimeMillis()-startTime;
      windowSize=20*windowSize/1000;
      ++sampleMode;

      logger.info("samples captured= %d; elapsed=%lld", savedSize, elapsed);
      logger.info("window size = %d", windowSize);


      if (savedSize > expectedSPS) {
        thread(cableMonitor).detach();
        return;
      }
      logger.info("retying...");
      usleep(1000*1000);
    }
    logger.error("Is your i2c bus overclocked?");
    char msg[2048];
    sprintf(msg,"SPS=%d, which is smaller than expected (%d).", savedSize, expectedSPS);
    bootError(msg);
}

int textBoxWidgetUpdate(gpointer data) {
    gtk_entry_set_text(GTK_ENTRY(degreeInputBox), degreeTextBox);
    return 0;
}

bool updateTimeFontSize=false;
PangoFontDescription *timeFont;
PangoFontDescription *dateFont;

int timeWidgetUpdate(gpointer data) {

    if (!updateTimeFontSize && screenHeight>screenBreakpoint) {
      updateTimeFontSize=true;
      timeFont = pango_font_description_new ();
      pango_font_description_set_family(timeFont,"DejaVu Sans Mono");
      pango_font_description_set_weight(timeFont, PANGO_WEIGHT_BOLD);
      pango_font_description_set_size(timeFont,22*PANGO_SCALE);

      dateFont = pango_font_description_new ();
      pango_font_description_set_family(dateFont,"Quicksand Light");
      pango_font_description_set_weight(dateFont, PANGO_WEIGHT_BOLD);
      pango_font_description_set_size(dateFont,18*PANGO_SCALE);


      auto attributes = gtk_label_get_attributes(utcTime);
      auto attr = pango_attr_font_desc_new(timeFont);
      pango_attr_list_change(attributes, attr);

      attributes = gtk_label_get_attributes(localTime);
      attr = pango_attr_font_desc_new(timeFont);
      pango_attr_list_change(attributes, attr);

      attributes = gtk_label_get_attributes(localDate);
      attr = pango_attr_font_desc_new(dateFont);
      pango_attr_list_change(attributes, attr);

      attributes = gtk_label_get_attributes(utcDate);
      attr = pango_attr_font_desc_new(dateFont);
      pango_attr_list_change(attributes, attr);
    }

    gtk_label_set_text(utcTime, utcTimeBuffer);
    gtk_label_set_text(utcDate, utcDateBuffer);
    
    gtk_label_set_text(localTime, localTimeBuffer);
    gtk_label_set_text(localDate, localDateBuffer);

    return 0;
}


void updateTextBox(float degree) {

    sprintf(degreeTextBox,"%.0f", degree);

    g_idle_add(textBoxWidgetUpdate, nullptr);
}

void clearTextBox() {

    degreeTextBox[0]=0;

    g_idle_add(textBoxWidgetUpdate, nullptr);
}


bool hitLimitSwitch() {
    int limitSwitch = digitalRead(options.LimitSwitch);
    if (limitSwitch==1) {
        logger.info("Limit switch triggered");
        forceVoltageDebugDisplay=true;
        return true;
    } else {
        return false;
    }
}


static void stopRotor(float newDegree) {   
    bool expected=false;
    if (!stoppingRotor.compare_exchange_weak(expected, true)) {
      return;
    }

    logger.info("stopping rotor indicator");
    neopixel_setPixel(operationIndicator, brakingColor);
    neopixel_render();
    delay(1);

    deactivateRotor();
    neopixel_setPixel(operationIndicator, stopColor);
    neopixel_render();
    
    if (logFile) fprintf(logFile,"parked\n");

    delay(1000);
    float targetDeviation=rotorDegree-newDegree;

    logger.info("rotor parked; rotorDegree=%3.0f; target deviation=%.1f", 
                    rotorDegree, targetDeviation);
    forceVoltageDebugDisplay=true;
    neopixel_setPixel(operationIndicator, stopColor);
    neopixel_render();

    forceCompassRedraw=true;

    if (logFile) {
        fclose(logFile);
        delay(20);
        logFile=nullptr;
    } 
    parked=true;
    stoppingRotor=false;
    clearTextBox();
}

static void moveRotorWorker(float degrees, float newDegree) {

    parked=false;
    skipWindow=true;
    skipTime=currentTimeMillis()+1000;
    if (!activateRotor(degrees)) {
        skipWindow=false;
        logger.error("failed to start rotor motor");
            return;
    }
    skipTime=currentTimeMillis()+300;
    logger.info("moving %.0f degrees to %.1f", degrees, newDegree);

    neopixel_setPixel(operationIndicator, movingColor);
    neopixel_render();

    usleep(50*1000); // debounce limit switch relay

    if (cwLimitPoint && degrees<0) {
        logger.info("leaving twilight zone");
        delay(3000);
        cwLimitPoint=false;
    }

    if (degrees>0) { // clockwise
        while (rotorDegree<(newDegree-2) && !hitLimitSwitch()) {
            usleep(250);  // 0.25 ms
        }
    } else {    // counter-clockwise
        while (rotorDegree>(newDegree+2) && !hitLimitSwitch()) {
            usleep(250);  // 0.25 ms
        }
    }
    stopRotor(newDegree);

}

static void moveRotor(float degrees) {
    float currentDegree=rotorDegree;
    if (isRotorMoving()) {
        logger.error("rotor is already moving...");
        return;
    }

    // if (!isRotorMotorReady()) {
    //     logger.error("the rotor motor reports 'not ready'.  Is the external turned power on?");
    //     return;
    // }

    auto newDegree=currentDegree+degrees;
    if (newDegree<0) {
        newDegree+=360;
    }
    if (newDegree>=360) {
        newDegree-=360;
    }

    if (abs(newDegree-currentDegree)<1.5) {
        logger.info("current degree=%.1f; requested degree=%.1f", currentDegree, newDegree);
        logger.info("movement degree is too small.  doing nothing");
        return;
    }
    
    thread(moveRotorWorker,degrees,newDegree).detach();
}
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
int main(int argc, char **argv) {
  GtkBuilder *uiBuilder;
  GObject    *button;
  GError     *error=nullptr;


  int rs=setuid(0);
  if (rs<0) {
      bootError("sorry, this app must run as root; check setuid bit");
  }

  makeConfigFolder();


  if (!options.commandLineOptions(argc, argv)) {
    exit(1);
  }
  debug=(logger.getGlobalLevel()<=DEBUG);

  displayParameters();

  if (wiringPiSetup() != 0) {
    bootError("wiringPi setup failed");
  }
  
  pinMode(options.LimitSwitch, INPUT);
  // doesn't work on RPi 4
  //pullUpDnControl(options.LimitSwitch, PUD_UP);

  a2dSetup();

  if (initRotorMotor()!=0) {
      bootError("rotor motor initializaion failed");
  }

  gtk_init(&argc, &argv);

  GtkCssProvider *cssProvider = gtk_css_provider_new();
  gtk_css_provider_load_from_path(cssProvider, "theme.css", NULL);

  gtk_style_context_add_provider_for_screen(gdk_screen_get_default(),
                              GTK_STYLE_PROVIDER(cssProvider),
                              GTK_STYLE_PROVIDER_PRIORITY_USER);

  /* Construct a GtkBuilder instance and load our UI description */
  uiBuilder = gtk_builder_new ();
  if (gtk_builder_add_from_file (uiBuilder, "layout.ui", &error) == 0) {
      g_printerr ("Error loading file: %s\n", error->message);
      g_clear_error (&error);
      return 1;
  }

  /* Connect signal handlers to the constructed widgets. */
  mainWindow = gtk_builder_get_object (uiBuilder, "window");
  g_signal_connect (mainWindow, "destroy", G_CALLBACK (programStop), NULL);

  button = gtk_builder_get_object (uiBuilder, "MoveExactButton");
  g_signal_connect (button, "clicked", G_CALLBACK (moveExact), NULL);

  button = gtk_builder_get_object (uiBuilder, "FastReverse");
  g_signal_connect (button, "clicked", G_CALLBACK (moveTenCounterClockwise), NULL);

  button = gtk_builder_get_object (uiBuilder, "FastForward");
  g_signal_connect (button, "clicked", G_CALLBACK (moveTenClockwise), NULL);


  button = gtk_builder_get_object (uiBuilder, "abort");
  g_signal_connect (button, "clicked", G_CALLBACK (abortMovement), NULL);

  drawingArea = (GtkWidget *) gtk_builder_get_object (uiBuilder, "CompassDrawingArea");
  g_signal_connect (mainWindow, "button-press-event", G_CALLBACK (compassClick), NULL);



  setButton(uiBuilder, "northButton", "clicked", G_CALLBACK(moveTo), &directional.north);
  setButton(uiBuilder, "southButton", "clicked", G_CALLBACK(moveTo), &directional.south);
  setButton(uiBuilder, "eastButton", "clicked", G_CALLBACK(moveTo),  &directional.east);
  setButton(uiBuilder, "westButton", "clicked", G_CALLBACK(moveTo),  &directional.west);

  setButton(uiBuilder, "seButton", "clicked", G_CALLBACK(moveTo), &directional.se);
  setButton(uiBuilder, "swButton", "clicked", G_CALLBACK(moveTo), &directional.sw);
  setButton(uiBuilder, "nwButton", "clicked", G_CALLBACK(moveTo), &directional.nw);
  setButton(uiBuilder, "neButton", "clicked", G_CALLBACK(moveTo), &directional.ne);




  degreeInputBox = (GtkWidget *) gtk_builder_get_object (uiBuilder, "DegreeInputBox");

  initTime(uiBuilder);

  createDrawingSurface(drawingArea);
  g_signal_connect (drawingArea,"configure-event", G_CALLBACK (configure_event_cb), NULL);
  g_signal_connect (drawingArea, "draw", G_CALLBACK (draw_cb), NULL);
  g_signal_connect (G_OBJECT(mainWindow), "window-state-event", G_CALLBACK(manualScreenRedraw), NULL);


  if (options.fullscreen) {
      logger.info("entering full screen mode");
      gtk_window_fullscreen(GTK_WINDOW(mainWindow));
  }

  getScreenResolution();
  readCalibration();
  
  thread(initializeTimezones).detach();
  thread(hideMouse).detach();
  thread(timeUpdate).detach();
  thread(renderCompass).detach();
  thread(initRotorDegrees).detach();
  thread(wifiUpdate).detach();
  neopixel_setup();

  gtk_main();

  return 0;
}
// #pragma clang diagnostic pop
#pragma GCC diagnostic pop
void stopMotor();

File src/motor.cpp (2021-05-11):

#include <wiringPi.h>

#include <stdio.h>
#include <stdlib.h>
#include <string.h>
#include <ctype.h>
#include <errno.h>
#include <unistd.h>
#include <log4pi.h>

#include "motor.h"
#include "Options.h"

#define RELAY_DEACTIVATED 1
#define RELAY_ACTIVATED   0

using namespace std;
using namespace common::utility;
using namespace common::synchronized;


powerType power = {
    -1, 1, 0
};

int powerSetting = power.automatic;


static Logger logger{"RotorMotor"};

static int   brakeStatus=-1;
static int64_t          startTime=-1;
static SynchronizedBool _isRotorMoving{false};
static bool _isRotorReallyMoving=false;

static float motorDirection=0;

int initRotorMotor() {
    logger.info("initializing motor");
    logger.debug("GPIO WiringPi motor pins:");
    logger.debug("    OutputEnable:     %2d", options.OutputEnable);
    logger.debug("    RotorPower:       %2d", options.RotorPower);
    logger.debug("    CW:               %2d", options.ClockwisePin);
    logger.debug("    CCW:              %2d", options.CCWPin);
    logger.debug("    BrakePin:         %2d", options.BrakePin);

    initPins();

    pinMode(options.BrakePin,         OUTPUT);
    pinMode(options.ClockwisePin,     OUTPUT);
    pinMode(options.CCWPin,           OUTPUT);
    pinMode(options.OutputEnable,     OUTPUT);
    pinMode(options.RotorPower,       OUTPUT);

    initPins();

    return 0;
}

void initPins() {
    digitalWrite(options.ClockwisePin,     RELAY_DEACTIVATED);
    digitalWrite(options.CCWPin,           RELAY_DEACTIVATED);
    digitalWrite(options.BrakePin,         RELAY_DEACTIVATED);
    digitalWrite(options.RotorPower,       RELAY_DEACTIVATED);
    digitalWrite(options.OutputEnable,     1);
}


bool isRotorMoving() {
    return _isRotorMoving.get();
}

bool isRotorReallyMoving() {
    return _isRotorReallyMoving;
}

void deactivateRotor() {
    digitalWrite(options.ClockwisePin,  RELAY_DEACTIVATED);
    digitalWrite(options.CCWPin,        RELAY_DEACTIVATED);

    if (!_isRotorMoving.get()) {
        digitalWrite(options.BrakePin,      RELAY_DEACTIVATED);
        digitalWrite(options.RotorPower,    RELAY_DEACTIVATED);
        return;
    }
    logger.debug("deactivating rotor motor");

    auto now = currentTimeMillis();
    long travelTime = now - startTime;
    if (startTime<0) {
        travelTime=0;
    }

    uint parkingDelay = 5000;

    if (travelTime<1000) {
        parkingDelay = 1000;
    }    

    _isRotorReallyMoving=false;

    logger.debug("parking delay=%u", parkingDelay);
    delay(parkingDelay);

    logger.debug("parking brake engaged");
    digitalWrite(options.BrakePin,      RELAY_DEACTIVATED);
    digitalWrite(options.RotorPower,    RELAY_DEACTIVATED);

    brakeStatus=RELAY_DEACTIVATED;

    _isRotorMoving.set(false);

    auto end = currentTimeMillis();
    long parkingTime = end - now;
    logger.info("travel elapsed time: %ld; parking time: %ld", travelTime, parkingTime);
}



bool isRotorMovingClockwise() {
    if (_isRotorMoving.get() && motorDirection>0) {
        return true;
    } else {
        return false;
    }
}

bool activateRotor(float direction) {
    motorDirection=direction;
    if (direction==0) {
        logger.error("requested motor move with direction of zero");
        return false;
    }

    if (!_isRotorMoving.commit(false,true)) {
        logger.error("rotor is already moving...");
        return false;
    }


    startTime = currentTimeMillis();

    const char *vector;
    int motorPin;

    digitalWrite(options.RotorPower, RELAY_ACTIVATED);
    delay(200);

    if (direction>0) {
        motorPin=options.ClockwisePin;
        vector="clockwise";
    } else {
        motorPin=options.CCWPin;
        vector="counter-clockwise";
    }

    logger.debug("actiating rotor motor %s; pin=%d", vector, motorPin);


    logger.debug("parking brake disengaged");
    digitalWrite(options.BrakePin, RELAY_ACTIVATED);
    brakeStatus=RELAY_ACTIVATED;
    _isRotorReallyMoving=true;

    delay(100);
    digitalWrite(motorPin, RELAY_ACTIVATED);
    return true;
}

int getBrakeStatus() {
    return brakeStatus;
}

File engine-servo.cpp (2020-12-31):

#include <wiringPi.h>
#include <pca9685.h>

#include <stdio.h>
#include <stdlib.h>
#include <string.h>
#include <ctype.h>
#include <errno.h>
#include <unistd.h>
#include <log4pi.h>

using namespace std;
using namespace common::utility;
using namespace common::synchronized;


static int pca9685fd = -1;

static int PCA9865_CAP      = 1400;
static int PCA9865_RES      = 4046;
static int PCA9865_ADDRESS  = 0x40;
static int pwmPin           = 8;
static int pwmFreq          = -1;

#define PCA9685_PIN_BASE 200

static bool debug = false;

static Logger logger{"RotorEngine"};

int  initRotorEngine() {
	if (int ret = wiringPiSetup()) {
		logger.error("Wiring Pi setup failed, ret=%d", ret);
		return 9;
	}

    if ((pca9685fd=pca9685Setup(PCA9685_PIN_BASE, PCA9865_ADDRESS, PCA9865_CAP)) <= 0) {
		logger.error("open pca9685 handle failed!");
		return 9;
	}

    return 0;
}

void setFrequency(int pin, int speed) {
	if (speed < 1) {
		speed = 0;
	} else if (speed >= 4096) {
		speed = 4096;
	}
	pwmWrite(PCA9685_PIN_BASE + pin, speed);
	if (debug) {
		printf("finished\n", pin, speed); fflush(stdout);
	}
}

void deactivateRotor() {
    setFrequency(pwmPin, 0);
}

void activateRotor(float direction) {
    setFrequency(pwmPin, 0);
    // if (direction==0) {
    //     return;
    // }

    // int f;
    // if (direction>0) {
    //     f=2500;
    // } else {
    //     f=3800;
    // }

    // setFrequency(pwmPin, f);
    // logger.info("freq=%d",f);
}

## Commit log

2020-11-30 fix text box locking
    [rotor.cpp]
2020-11-30 updated move rotor
2020-11-30 fix compass background transparency
    [rotor.cpp]
2020-12-01 added directional buttons
2020-12-31 multi-threaded gtk
2020-12-31 move rotor diagnosits
2020-12-31 adjust motor controll
2020-12-31 adjust increment buttons to match wobble limit
    [rotor.cpp]
2020-12-31 fix 100% cpu usage
    [rotor.cpp]
2020-12-31 new engine code for actual rotor
2020-12-31 separate rotor Vs from mcp3008 reference voltage
2021-01-01 update engine relay states
2021-01-03 move sync strategy to motor.cpp & added command line parameter for selecting channel
2021-01-06 circuit diagram
2021-01-07 update resistor values
2021-01-07 update circuit diagram
2021-01-07 update circuit diagram title
2021-01-07 add options for a2c channels and resistors
2021-01-10 add 24v relay to circuit digram
2021-01-12 made the pins on I2C LLC match the physical device
2021-04-05 updated parking brake debug statements
2021-04-19 external power
2021-04-25 15v working
2021-04-26 added rotor power
2021-04-26 add bcm/hdr pinout numbers to source enum "RotorPin"
2021-05-08 trap interrupt
2021-05-09 max volts adjustment
2021-05-10 fix power issue
2021-05-11 abort button
2021-05-15 Add files via upload
    500 ohm aspect indicator variable resistor
2021-05-25 read voltage update
2021-05-27 fine tune sample period
2021-06-06 new resistor value & gain
2021-06-07 cable disconnected dialog
2021-06-07 add skip window to smooth starts
    [Options.h, rotor.cpp]
2021-06-07 hide mouse on boot error
    [rotor.cpp]
2021-06-07 fixed braking stop color delay
    [rotor.cpp]
2021-06-07 fix timezone min height for small screens
    [rotor.cpp]
2021-06-14 fix show realized ip delay
    [rotor.cpp]
2021-06-14 realized ip disappearance fixed
    [rotor.cpp]
2021-06-14 fix ssid selection tab change
    [rotor.cpp]
2021-06-20 calibration screen
2021-06-21 thread neopixel color test
2021-06-21 fix button aspect ratio
2021-07-04 move parts list to google sheets
    [parts list.xlsx]
2021-09-27 limit switch detection update
2021-09-29 limit switch detection circuit scope screenshots
2021-10-16 low pass filter wire diagram
    [transistor logic.xlsx]
2021-10-17 update circuit diagram - ads1115 alert ready
2021-10-17 change default resistor
2022-10-01 print resistor values
2023-02-27 rotor manual
2023-03-04 eagle cad
    [rotor.border.dxf, rotor.brd, rotor.dxf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]
2023-03-05 eagle-initial version
    [rotor.brd, rotor.sch]
2023-03-05 add dpdt switch
    [rotor.brd, rotor.sch]
2023-03-17 rotor v1.01
    [rotor.border.dxf, rotor.brd, rotor.dxf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]
2023-03-18 fix rotor input resistor
    [console.border.dxf, console.brd, console.dxf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]
2023-03-18 v1.02 - fix transistors
    [rotor.brd, rotor.sch]
2023-10-08 2n2222 diagram
    [hat.border.dxf, rotor.brd, rotor.sch]

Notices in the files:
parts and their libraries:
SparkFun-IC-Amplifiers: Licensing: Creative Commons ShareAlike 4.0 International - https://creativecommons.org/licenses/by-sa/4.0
